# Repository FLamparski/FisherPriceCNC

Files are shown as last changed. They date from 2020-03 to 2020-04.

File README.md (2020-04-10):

# Fisher Price CNC

A desktop, 2D CNC machine made from parts salvaged from a
really terrible 3D priner. This repository contains the
phyiscal CAD design of the machine, electrical and electronic
schematics for any custom boards, and any extra code to make it
run (unlikely to be needed but you never know).

More documentation is currently available on the following
Trello board: https://trello.com/b/17SHQEqY/fisher-price-cnc

## Physical designs - OpenSCAD  - `/scad`

The machine is designed with OpenSCAD, a CAD program that does
away with all of this "drawing" nonsense and instead lets you
use a C-ish programming language to do geometry. The upshot
is that you could treat it like any old source file in git, and
you also have a fairly well understood model for including
libraries.

Speaking of libraries, you will need them. Please install the
following to your OpenSCAD libraries folder:

* [NopSCADlib](https://github.com/nophead/NopSCADlib)

### Assembly instructions

The project leverages NopSCADlib's autogenerated assembly instructions and asset generation. The
instructions are in [`ASSEMBLY.md`](ASSEMBLY.md). Note that these might be a bit variable in quality,
please open an issue if something's not clear. I intend on creating more detailed instructions
towards the end of the project.

To regenerate the assembly instructions, STLs, images, and the bill of materials, use `make_all.ps1`.

## Firmware

This machine uses GRBL v1.1 as its firmware. There is a configuration file, `grbl_config.h`, that is
required to compile and upload GRBL and have it work correctly - it needs to disable homing on the
Z axis because the Z axis does not exist.

Copy the `grbl_config.h` on top of the `config.h` in whatever location you have installed GRBL,
and then reflash through the Arduino IDE.

## Attribution

A number of the parts and a lot of the code for this machine
has been borrowed from other projects. Here's a list:

* Some phyiscal parts have been reused or adapted from the [Prusa i3 MK3s](https://github.com/prusa3d/Original-Prusa-i3/tree/MK3S/Printed-Parts/SCAD) (GPLv3)
* [GRBL](https://github.com/gnea/grbl) is currently used as firmware (GPLv3)

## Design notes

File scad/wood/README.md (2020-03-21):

These parts are not from the normal build, but rather
to fit 30x16 strips of MDF that I found around the flat
and decided to use before ordering the extrusions.

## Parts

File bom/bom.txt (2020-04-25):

Vitamins:
                               X                        
                                                        
                               m                        
                               o           Y            
                               t  X              Y      
                               o        Y  c           Y
    E           L              r  m        a     l  Y   
    l  E  E     a                 o     a  r     i     m
    e  l  l     s        X     a  t     x  r     m  m  o
       e  e     e              n  o     i  i     i  o  t
    b     c     r        c     d  r     s  a     t  t  o
    o  b  t              a  X              g  Y     o  r
    x  o  r     m     X  r     p  h  Y  h  e     s  r   
       x  o  F  o        r  i  u  o     o     i  w     r
 B  b     n  r  d  M  a  i  d  l  l  a  l  b  d  i  l  i
 a  a  t  i  o  u  a  x  a  l  l  d  x  d  a  l  t  e  g
 c  s  o  c  n  l  i  i  g  e  e  e  i  e  s  e  c  f  h
 k  e  p  s  t  e  n  s  e  r  y  r  s  r  e  r  h  t  t
  |  |  |  |  |  |  |  |  |  | 1|  |  |  |  |  |  |  |  |  1 Stepper motor NEMA17 x 40mm
  |  |  |  |  |  |  |  |  |  |  |  |  |  |  |  |  | 1| 1|  2 Stepper motor NEMA17 x 34mm
  |  |  |  |  |  | 2|  |  |  |  |  |  |  |  |  |  |  |  |  2 Belt GT2 x 6mm x 814mm
 1|  |  |  | 1|  |  |  |  |  |  |  |  |  |  |  |  |  |  |  2 Extrusion E3030 x 445mm
  |  |  |  |  |  |  |  |  |  |  |  | 2|  |  |  |  |  |  |  2 Extrusion E3060 x 345mm
  |  |  |  |  |  | 4|  |  |  |  |  |  |  |  |  |  |  |  |  4 Extrusion corner bracket 20
  |  |  |  |  | 1|  |  |  |  |  |  |  |  |  |  |  |  |  |  1 Fan 40mm x 11mm
  |  |  | 1|  |  |  |  |  |  |  |  |  |  |  |  |  |  |  |  1 Terminal block 2 way 3.5mm
  |  |  |  |  | 1|  |  |  |  |  |  |  |  |  |  |  |  |  |  1 laser module
  |  | 1|  |  |  |  |  |  |  |  |  |  |  |  |  |  |  |  |  1 LED 5 mm red
  |  |  |  |  |  |  |  | 2|  |  |  |  |  | 6|  |  |  |  |  8 Linear bearing LM8UU
  |  |  |  |  |  |  |  |  | 1|  | 1|  |  |  |  | 4|  |  |  6 Microswitch SS-01 or SS-5GL
  | 4|  |  |  |  |  |  |  |  |  |  |  |  |  |  | 8|  |  | 12 Nut M2 x 1.6mm 
  | 3|  |  |  |  |  |  | 2|  |  |  |  |  | 2|  |  |  |  |  7 Nut M3 x 2.4mm 
  | 3|  |  |  |  |  |  | 1|  |  |  |  |  |12|  |  |  |  | 16 Nut M3nS 5.5 x 1.8mm 
  |  |  |  |  |  |  |  |  | 1|  |  |  |  |  | 2|  |  |  |  3 Nut M4 x 3.2mm 
  |  |  | 1|  |  |  |  |  |  |  |  |  |  |  |  |  |  |  |  1 Arduino Uno R3
  |  |  | 4|  |  |  |  |  |  |  |  |  |  |  |  |  |  |  |  4 Stepper Motor Driver
  |  |  | 1|  |  |  |  |  |  |  |  |  |  |  |  |  |  |  |  1 Perfboard 80 x 20mm
  |  |  | 8|  |  |  |  |  |  |  |  |  |  |  |  |  |  |  |  8 Pin socket 8 x 1
  |  |  |  |  |  |  |  |  | 1|  |  |  |  |  | 2|  |  |  |  3 Pulley GT2 idler 20 teeth
  |  |  |  |  |  |  |  |  |  | 1|  |  |  |  |  |  | 1| 1|  3 Pulley GT2OB 20 teeth
  |  |  |  |  |  |  |  |  |  |  |  |  | 8|  |  |  |  |  |  8 Smooth rod 8mm x 30mm
  |  |  |  |  |  |  | 2|  |  |  |  |  |  |  |  |  |  |  |  2 Smooth rod 8mm x 343mm
  |  |  |  |  |  |  |  |  |  |  |  | 4|  |  |  |  |  |  |  4 Smooth rod 8mm x 345mm
  |  |  |  |  |  |  |  |  |  |  |  |  |  |  |  | 8|  |  |  8 Screw M2 cap x 10mm
  |  |  |  |  |  |  |  | 2|  |  |  |  |  |  |  |  |  |  |  2 Screw M3 cap x 12mm
  |  |  |  |  |  |  |  | 1|  |  |  |  |  |  |  |  |  |  |  1 Screw M3 cap x 20mm
  |  |  |  |  |  |  |  |  |  |  |  |  |  | 4|  |  |  |  |  4 Screw M3 cap x  6mm
  |  |  |  |  |  |  |  |  |  |  | 3|  |  |  |  |  | 4| 4| 11 Screw M3 cap x  8mm
  |  |  |  |  |  |  |  |  |  | 2|  |  |  |  |  |  |  |  |  2 Screw M3 grub x  6mm
  |  |  |  |  |  |  |  | 3|  |  |  |  |  |  |  |  |  |  |  3 Screw M3 pan x 12mm
  |  |  |  |  |  |  |  | 1|  |  |  |  |  |  |  |  |  |  |  1 Screw M3 pan x  5mm
  |  |  | 3|  |  | 2|  |  |  |  |  |  |  |  |  |  |  |  |  5 Screw M3 pan x  8mm
  |  |  |  |  |  |  |  |  |  |  |  |  | 8|  | 4|  | 2| 2| 16 Screw M4 cap x 10mm
  |  |  |  |  |  |  |  |  | 1|  |  |  |  |  | 2|  |  |  |  3 Screw M4 cap x 20mm
  |  |  |  |  |  | 8|  |  |  |  |  |  |  |  |  | 8|  |  | 16 Screw M4 cap x  8mm
  |  |  |  |  |  |  |  |  |  |  |  |  |  |  |  | 8|  |  |  8 Nut M4 hammer
  |  |  |  |  |  | 8|  |  |  |  |  |  | 8|  | 4|  | 2| 2| 24 Nut M4 sliding T
  |  |  |  |  |  |  |  |  |  |  |  |  |  |  |  |  | 4| 4|  8 Washer star M3 x 0.5mm
  |  | 1|  |  |  |  |  |  |  |  |  |  |  |  |  |  |  |  |  1 Toggle switch CK7101
  |  |  |  |  |  |  |  |  |  |  |  |  |  |  |  |  | 4| 4|  8 Washer  M3 x 7mm x 0.5mm
  |  |  |  |  |  | 8|  |  | 2|  |  |  |  |  | 4|  |  |  | 14 Washer  M4 x 9mm x 0.8mm
  |  |  |  |  |  |  |  | 1|  |  |  |  |  |  |  |  |  |  |  1 Ziptie 2.5mm x 100mm min length
  |  |  |  |  |  |  |  |  |  |  |  |  | 8|  |  |  |  |  |  8 Ziptie 2.5mm x 100mm min length

Printed:
  | 1|  |  |  |  |  |  |  |  |  |  |  |  |  |  |  |  |  |  1 ele_box_base.stl
  |  | 1|  |  |  |  |  |  |  |  |  |  |  |  |  |  |  |  |  1 ele_box_top.stl
 1|  |  |  |  |  |  |  |  |  |  |  |  |  |  |  |  |  |  |  1 ele_bracket.stl
  |  |  |  |  |  |  |  | 1|  |  |  |  |  |  |  |  |  |  |  1 laser_wire_holder.stl
  |  |  |  |  |  |  |  | 1|  |  |  |  |  |  |  |  |  |  |  1 x_carriage_back.stl
  |  |  |  |  |  |  |  | 1|  |  |  |  |  |  |  |  |  |  |  1 x_carriage_front.stl
  |  |  |  |  |  |  |  |  | 1|  |  |  |  |  |  |  |  |  |  1 x_idler.stl
  |  |  |  |  |  |  |  |  |  |  | 1|  |  |  |  |  |  |  |  1 x_motor_holder_mount.stl
  |  |  |  |  |  |  |  |  |  |  |  |  | 8|  |  |  |  |  |  8 y_axis_holder.stl
  |  |  |  |  |  |  |  |  |  |  |  |  |  | 2|  |  |  |  |  2 y_carriage_base.stl
  |  |  |  |  |  | 2|  |  |  |  |  |  |  |  |  |  |  |  |  2 y_carriage_belt_clamp.stl
  |  |  |  |  |  |  |  |  |  |  |  |  |  |  | 2|  |  |  |  2 y_idler.stl
  |  |  |  |  |  |  |  |  |  |  |  |  |  |  |  | 4|  |  |  4 y_limit_switch.stl
  |  |  |  |  |  |  |  |  |  |  |  |  |  | 2|  |  |  |  |  2 y_limit_switch_hitter.stl
  |  |  |  |  |  |  |  |  |  |  |  |  |  |  |  |  | 1|  |  1 y_motor_left_mount.stl
  |  |  |  |  |  |  |  |  |  |  |  |  |  |  |  |  |  | 1|  1 y_motor_right_mount.stl

Assemblies:
  1 back_assembly
  1 ele_box_base_assembly
  1 ele_box_top_assembly
  1 electronics_assembly
  1 front_assembly
  1 laser_module_assembly
  1 main_assembly
  1 x_axis_assembly
  1 x_carriage_assembly
  1 x_idler_assembly
  1 x_motor_and_pulley_assembly
  1 x_motor_holder_assembly
  2 y_axis_assemblies
  8 y_axis_holder_assemblies
  2 y_carriage_base_assemblies
  2 y_idler_assemblies
  4 y_limit_switch_assemblies
  1 y_motor_left_assembly
  1 y_motor_right_assembly

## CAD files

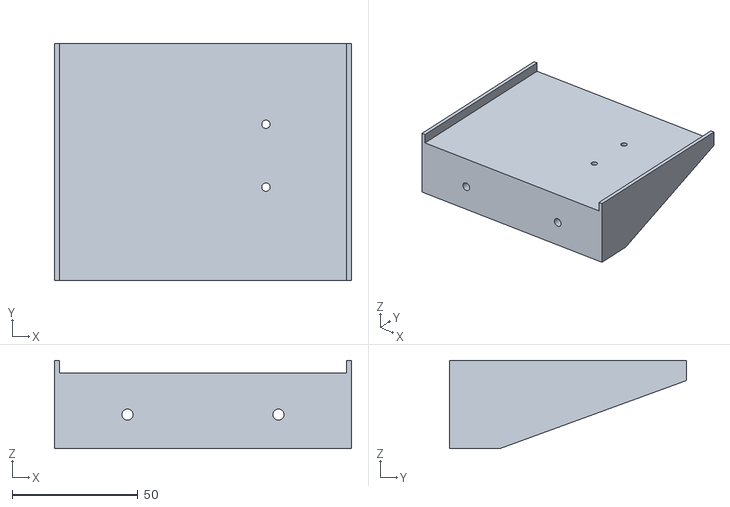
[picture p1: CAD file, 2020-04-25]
stls/ele_bracket.stl
118.0 x 94.0 x 35.0

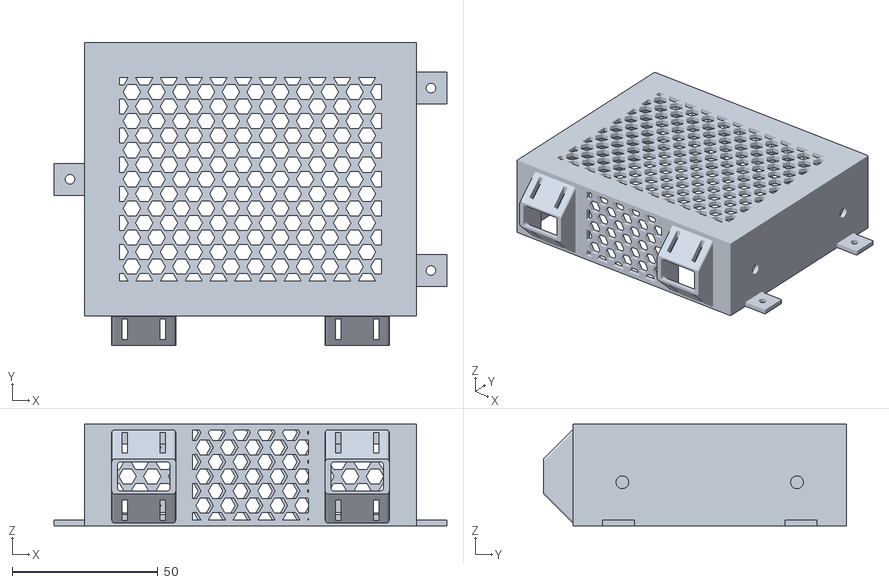
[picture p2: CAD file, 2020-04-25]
stls/ele_box_top.stl
135.0 x 104.1 x 35.0

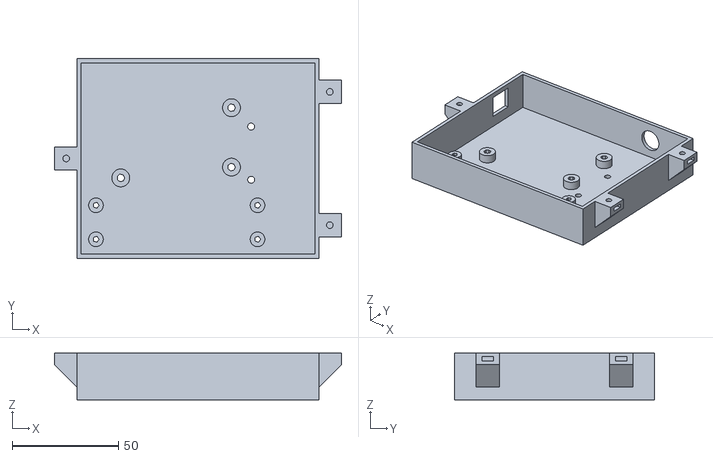
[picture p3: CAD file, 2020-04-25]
stls/ele_box_base.stl
135.0 x 94.0 x 22.0

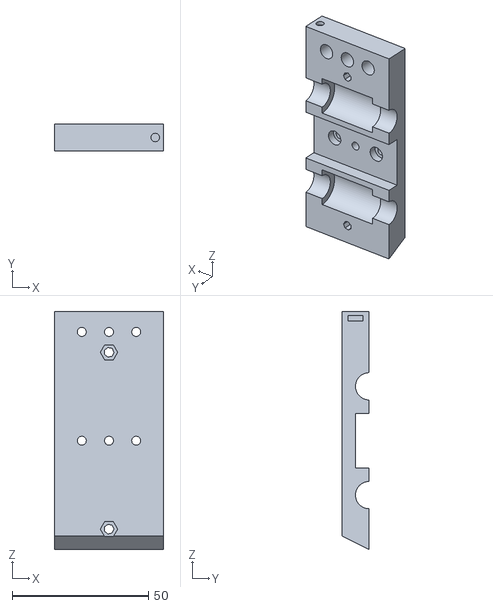
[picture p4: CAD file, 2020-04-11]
stls/x_carriage_front.stl
40.0 x 10.0 x 87.5

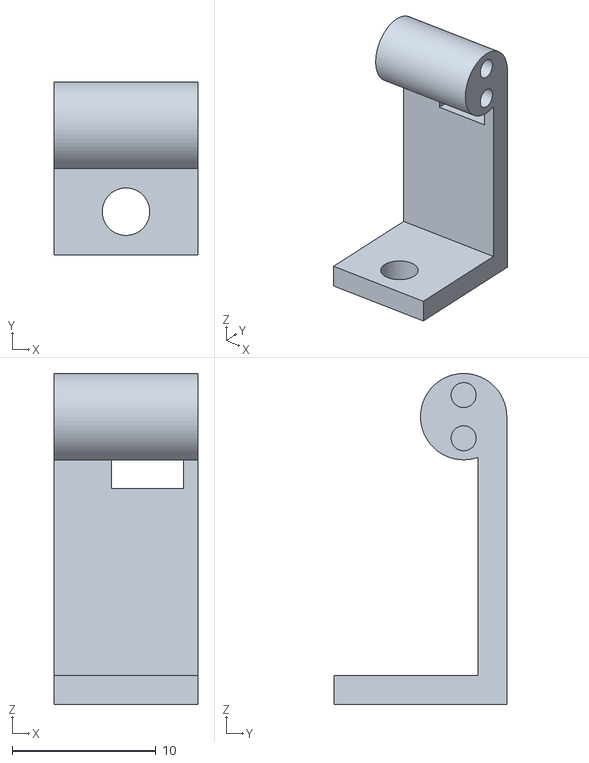
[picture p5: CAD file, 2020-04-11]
stls/laser_wire_holder.stl
10.0 x 12.0 x 23.0

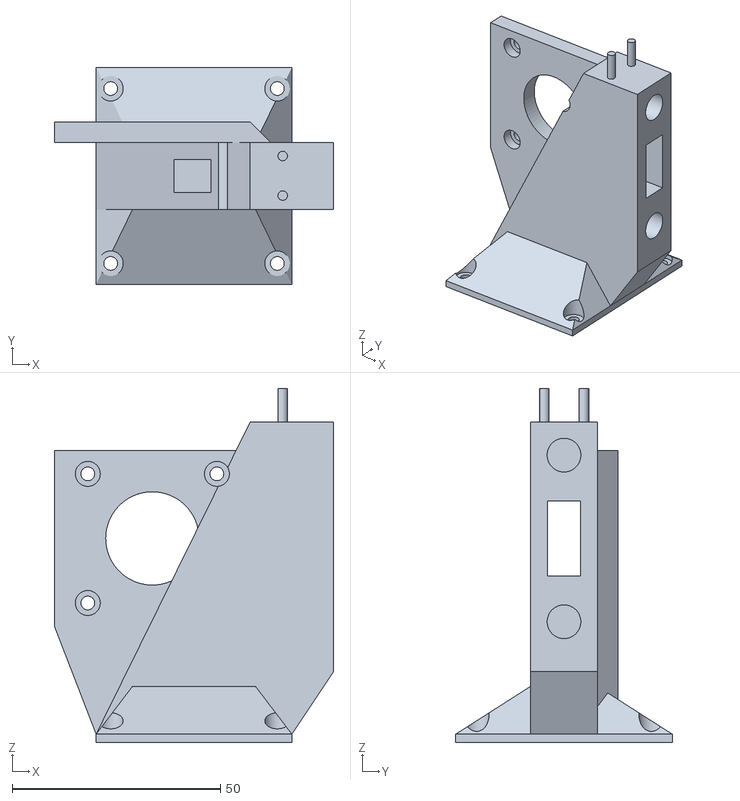
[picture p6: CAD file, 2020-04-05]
stls/x_motor_holder_mount.stl
67.0 x 52.0 x 85.0

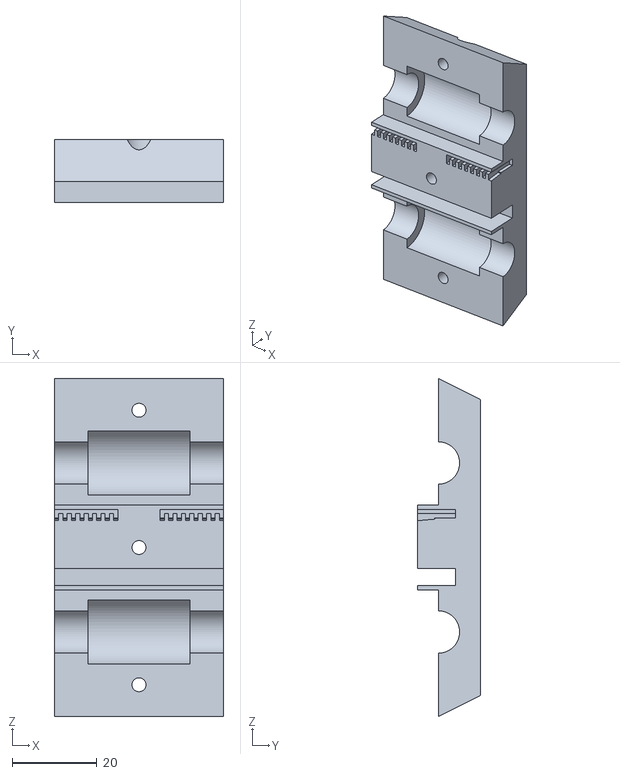
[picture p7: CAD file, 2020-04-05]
stls/x_carriage_back.stl
40.0 x 15.0 x 80.0

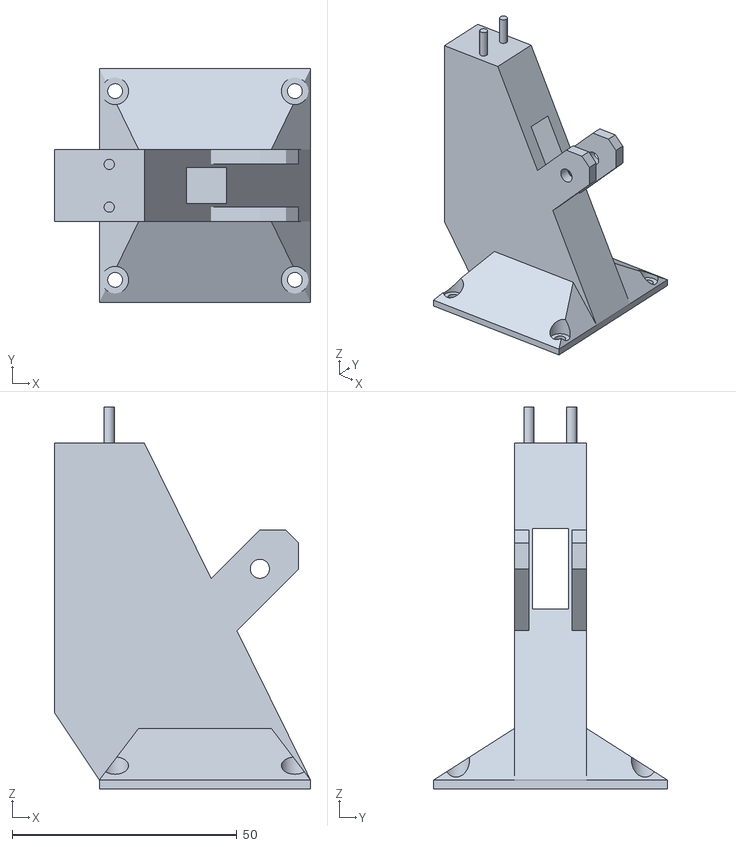
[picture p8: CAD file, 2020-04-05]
stls/x_idler.stl
57.0 x 52.0 x 85.0

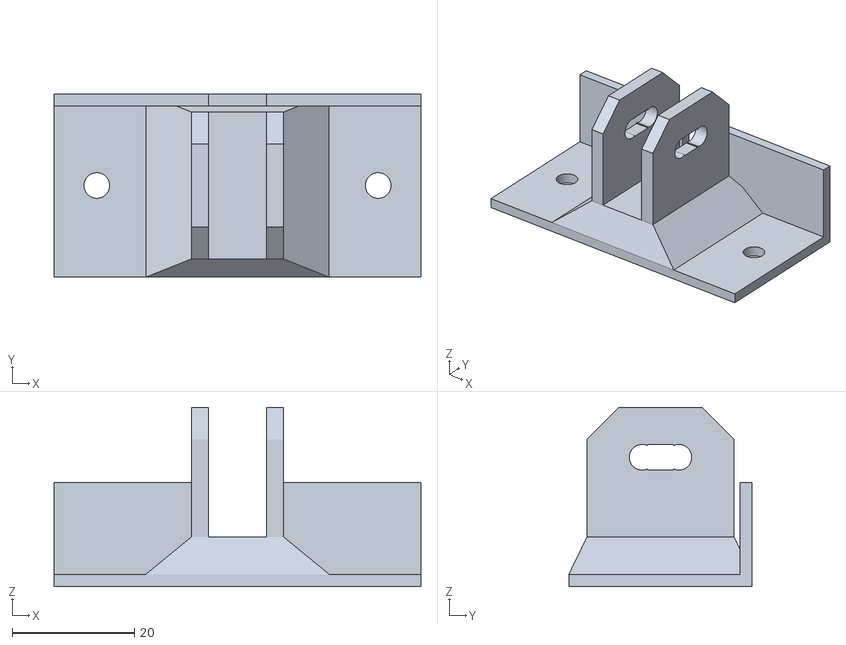
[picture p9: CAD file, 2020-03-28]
stls/y_idler.stl
60.0 x 30.0 x 29.3

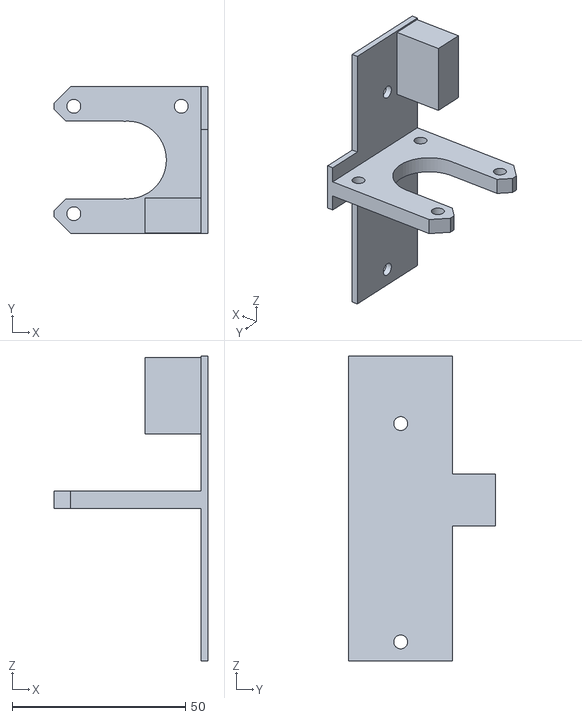
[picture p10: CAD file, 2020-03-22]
stls/y_motor_right_mount.stl
44.3 x 42.3 x 88.0

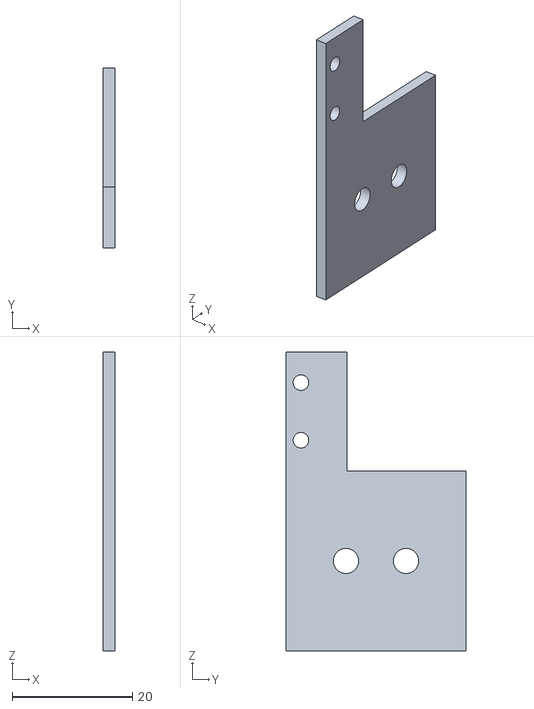
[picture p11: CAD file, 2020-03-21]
stls/y_limit_switch.stl
2.00 x 30.0 x 49.8

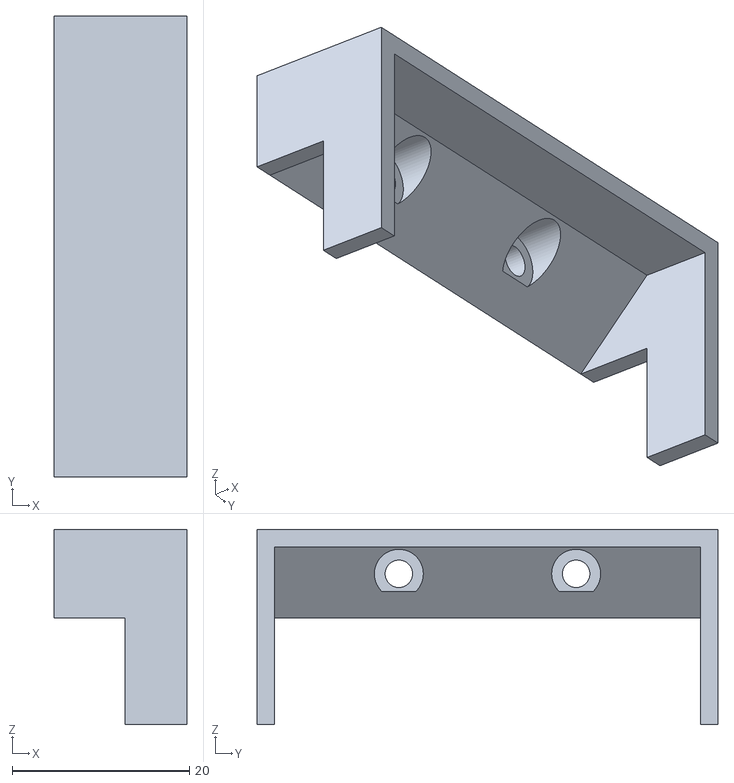
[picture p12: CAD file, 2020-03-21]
stls/y_limit_switch_hitter.stl
15.0 x 52.0 x 22.0

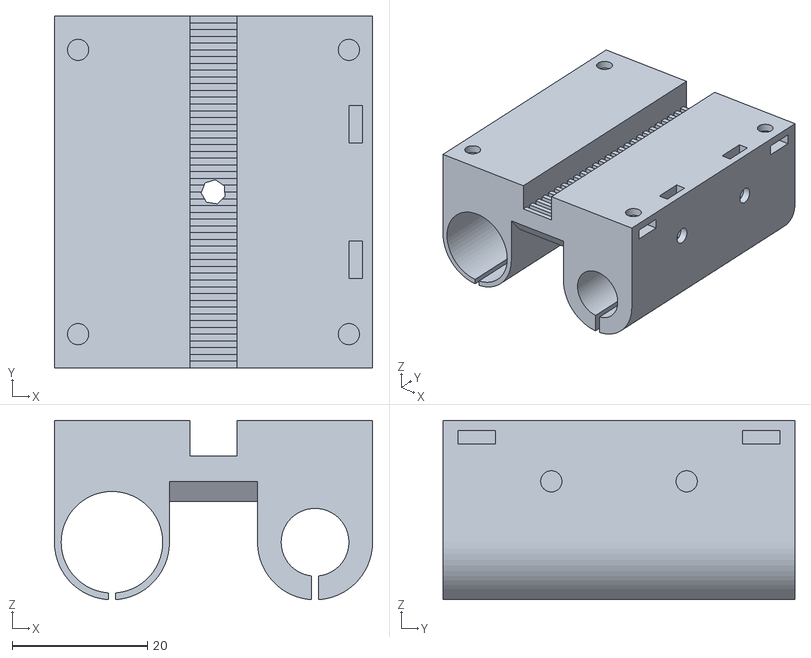
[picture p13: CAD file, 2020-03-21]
stls/y_carriage_base.stl
47.0 x 52.0 x 26.5

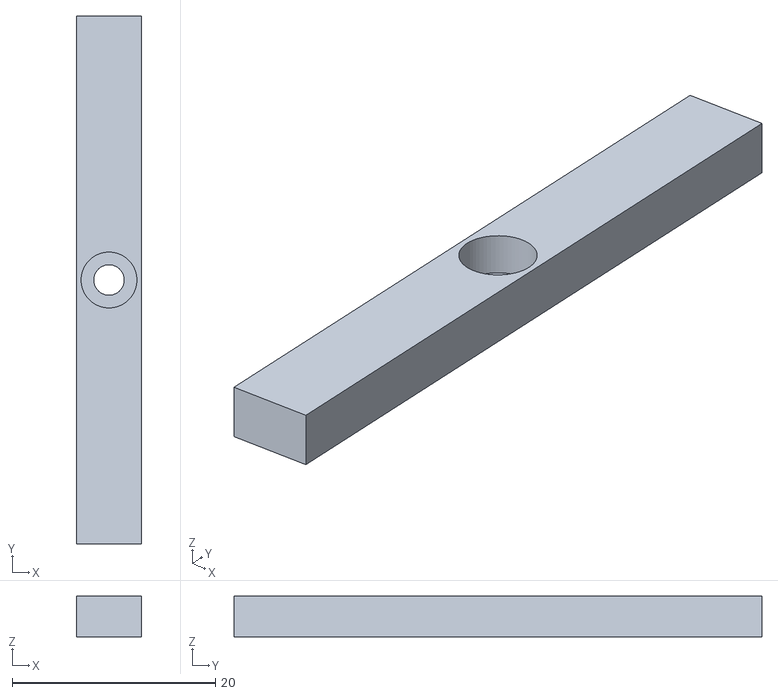
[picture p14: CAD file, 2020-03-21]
stls/y_carriage_belt_clamp.stl
6.40 x 52.0 x 4.00

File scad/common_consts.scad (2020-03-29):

include <NopSCADlib/core.scad>
include <NopSCADlib/vitamins/extrusions.scad>

printed_part_color = "orange";

y_holder_rod_offset = 9 + 8 - 0.5;

rod_length_mm = 345;
inner_margin = -10;
extrusion_type = E3030;
double_width_extrusion_type = E3060;

ew = extrusion_width(extrusion_type);
inner_width = rod_length_mm + inner_margin * 2;
outer_width = inner_width + 2 * 2 * ew;

echo(str("outer_width = ", outer_width));

layer_height = 0.2;

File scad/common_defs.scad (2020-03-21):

include <NopSCADlib/vitamins/nuts.scad>

module pyramid(dim_bottom, dim_top, h) {
    difference() {
        cube(concat(dim_bottom, h));

        x_diff = (dim_bottom[0] - dim_top[0]) / 2;
        x_angle = atan(h / x_diff);
        x_h_diff = sin(x_angle) / x_diff + 10;
        
        rotate([0, 90 - x_angle, 0])
        translate([-dim_bottom[0], 0, 0])
        cube([dim_bottom[0], dim_bottom[1], h + x_h_diff]);

        translate([dim_bottom[0], 0, 0])
        rotate([0, -(90 - x_angle), 0])
        cube([dim_bottom[0], dim_bottom[1], h + x_h_diff]);

        y_diff = (dim_bottom[1] - dim_top[1]) / 2;
        y_angle = atan(h / y_diff);
        y_h_diff = sin(y_angle) / y_diff + 10;
        
        translate([0, dim_bottom[1], 0])
        rotate([90 - y_angle, 0, 0])
        cube([dim_bottom[0], dim_bottom[1], h + y_h_diff]);

        rotate([-(90 - y_angle), 0, 0])
        translate([0, -dim_bottom[1], 0])
        cube([dim_bottom[0], dim_bottom[1], h + y_h_diff]);
    }
}

module square_nut_trap(type, length = 10, depth = 100) {
    width = nut_square_width(type);
    height = nut_square_thickness(type) + layer_height;
    screw_r = nut_square_size(type) / 2;

    union() {
        translate([-width / 2, -width / 2])
        cube([width, length, height]);
        cylinder(r1 = screw_r * 1.05, r2 = screw_r, h = depth);
    }
}

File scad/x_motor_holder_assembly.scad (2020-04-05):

include <NopSCADlib/core.scad>
include <NopSCADlib/vitamins/screws.scad>
include <NopSCADlib/vitamins/stepper_motors.scad>
include <NopSCADlib/vitamins/pulleys.scad>

include <common_consts.scad>
include <common_defs.scad>
include <x_axis_common.scad>

use <y_carriage_base_assembly.scad>

motor_tx = [-10, 13, rod_z_base + x_rods_pitch / 2];

module x_motor_holder_mount_stl() {
    stl("x_motor_holder_mount");

    difference() {
        translate([-y_carriage_base_width() / 2, -y_carriage_base_length() / 2, 0])
        union() {
            x_end_base();

            // support for the motor
            motor_bottom = rod_z_base + x_rods_pitch / 2 - NEMA_width(NEMA17M) / 2;
            motor_top = motor_bottom + NEMA_width(NEMA17M);
            motor_mount_y = x_gantry_thickness / 2 + y_carriage_base_length() / 2 + 5;
            translate([0, motor_mount_y, 0])
            rotate([90, 0, 0])
            linear_extrude(5) {
                polygon([
                    [0, base_thickness],
                    [-10, motor_bottom],
                    [-10, motor_top],
                    [y_carriage_base_width() - 10, motor_top],
                    [y_carriage_base_width() - 10, base_thickness]
                ]);
            }

            // mostly for looks
            translate([y_carriage_base_width() - 5, x_gantry_thickness / 2 + y_carriage_base_length() / 2 + 5, 0])
            rotate([0, 0, 180])
            linear_extrude(motor_top) {
                polygon([
                    [0, 5],
                    [5, 5],
                    [5, 0]
                ]);
            }
        }

        // mounting holes for the motor
        translate([-10, 13, rod_z_base + x_rods_pitch / 2])
        rotate([90, 0, 0]) {
            rbig = NEMA_big_hole(NEMA17M);
            cylinder(r=rbig, h=10, center=true);

            // TODO: make these adjustable?
            NEMA_screw_positions(NEMA17M, n = 3) {
                cylinder(r = screw_clearance_radius(M3_cap_screw), h = 10, center = true);

                translate([0, 0, 12])
                cylinder(r = screw_head_radius(M3_cap_screw) + 0.25, h = 20, center = true);
            }
        }
    }
}

module x_motor_and_pulley_assembly()
assembly("x_motor_and_pulley") {
    NEMA(NEMA17M);

    translate([0, 0, 13])
    pulley_assembly(GT2x20ob_pulley);
}

module x_motor_holder_assembly()
assembly("x_motor_holder") {
    color(printed_part_color)
    x_motor_holder_mount_stl();

    translate(motor_tx)
    rotate([90, 0, 0]) {
        x_motor_and_pulley_assembly();

        NEMA_screw_positions(NEMA17M, n = 3) {
            translate([0, 0, 4])
            screw(M3_cap_screw, 8);
        }
    }

    // Limit switch
    translate([23.9, 0, x_max_height + microswitch_thickness(medium_microswitch) - 1.2])
    rotate([0, 0, -90])
    microswitch(medium_microswitch);
}

if ($preview) {
    x_motor_holder_assembly();
}

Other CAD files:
stls/y_motor_left_mount.stl
stls/y_axis_holder.stl
scad/y_motor_assembly.scad
scad/back_assembly.scad
scad/electronics_assembly.scad
scad/front_assembly.scad
scad/laser.scad
scad/main_assembly.scad
scad/parts/frame_assembly.scad
scad/parts/y_axis_holder_assembly.scad
scad/parts/y_rod_assembly.scad
scad/square_nut_lug.scad
scad/wood/angle_bracket.scad
scad/x_axis_assembly.scad
scad/x_axis_common.scad
scad/x_carriage_assembly.scad
scad/x_idler_assembly.scad
scad/y_axis_assembly.scad
scad/y_axis_holder_assembly.scad
scad/y_carriage_base_assembly.scad
scad/y_idler_assembly.scad
scad/y_limit_switch_assembly.scad
scad/y_rod_assembly.scad

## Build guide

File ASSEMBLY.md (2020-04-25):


# Fisher Price CNC
Fisher Price CNC is a project to turn some parts from the world's worst 3D printer
into a reasonable CNC machine (probably a laser engraver of sorts).

Mechanical parts can be printed out of PLA for testing and PETG for production use.

List of purchases:
* Arduino + GRBL shield + motor drivers: https://smile.amazon.co.uk/gp/product/B06XJKVLG3/
* Belts: https://smile.amazon.co.uk/gp/product/B07JGXG7S2/
* Cap (hex) screws (M2/M3/M4): https://smile.amazon.co.uk/gp/product/B07KCT2F6K/
* M3 square nuts: https://smile.amazon.co.uk/gp/product/B075YSD5TN/
* Pan (phillips) screws (M3): https://smile.amazon.co.uk/gp/product/B07FTDRZRZ/
* LM8UU linear bearings: https://www.ebay.co.uk/itm/LM8UU-8mm-Linear-Bearing-for-Precision-shafts-3D-Printer-CNC-machine/124087391637

If you do not have a Monoprice Mini Delta, you will also need to buy:
* 6x 345x8mm smooth rods, preferably steel
* 3x NEMA17 stepper motors

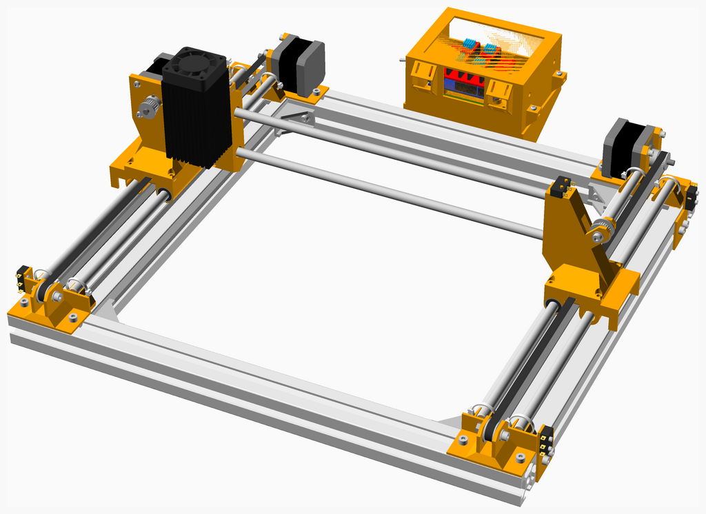
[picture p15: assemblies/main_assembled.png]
Main Assembly


## Table of Contents
1. [Parts list](#Parts_list)
1. [Laser Module Assembly](#laser_module_assembly)
1. [X Carriage Assembly](#x_carriage_assembly)
1. [X Idler Assembly](#x_idler_assembly)
1. [X Motor And Pulley Assembly](#x_motor_and_pulley_assembly)
1. [X Motor Holder Assembly](#x_motor_holder_assembly)
1. [X Axis Assembly](#x_axis_assembly)
1. [Ele Box Top Assembly](#ele_box_top_assembly)
1. [Ele Box Base Assembly](#ele_box_base_assembly)
1. [Electronics Assembly](#electronics_assembly)
1. [Y Motor Right Assembly](#y_motor_right_assembly)
1. [Y Motor Left Assembly](#y_motor_left_assembly)
1. [Back Assembly](#back_assembly)
1. [Y Idler Assembly](#y_idler_assembly)
1. [Front Assembly](#front_assembly)
1. [Y Carriage Base Assembly](#y_carriage_base_assembly)
1. [Y Limit Switch Assembly](#y_limit_switch_assembly)
1. [Y Axis Holder Assembly](#y_axis_holder_assembly)
1. [Y Axis Assembly](#y_axis_assembly)
1. [Main Assembly](#main_assembly)

## Parts list
| <span style="writing-mode: vertical-rl; text-orientation: mixed;">Laser&nbsp;Module</span> | <span style="writing-mode: vertical-rl; text-orientation: mixed;">X&nbsp;Carriage</span> | <span style="writing-mode: vertical-rl; text-orientation: mixed;">X&nbsp;Idler</span> | <span style="writing-mode: vertical-rl; text-orientation: mixed;">X&nbsp;Motor&nbsp;And&nbsp;Pulley</span> | <span style="writing-mode: vertical-rl; text-orientation: mixed;">X&nbsp;Motor&nbsp;Holder</span> | <span style="writing-mode: vertical-rl; text-orientation: mixed;">X&nbsp;Axis</span> | <span style="writing-mode: vertical-rl; text-orientation: mixed;">Ele&nbsp;Box&nbsp;Top</span> | <span style="writing-mode: vertical-rl; text-orientation: mixed;">Ele&nbsp;Box&nbsp;Base</span> | <span style="writing-mode: vertical-rl; text-orientation: mixed;">Electronics</span> | <span style="writing-mode: vertical-rl; text-orientation: mixed;">Y&nbsp;Motor&nbsp;Right</span> | <span style="writing-mode: vertical-rl; text-orientation: mixed;">Y&nbsp;Motor&nbsp;Left</span> | <span style="writing-mode: vertical-rl; text-orientation: mixed;">Back</span> | <span style="writing-mode: vertical-rl; text-orientation: mixed;">Y&nbsp;Idler</span> | <span style="writing-mode: vertical-rl; text-orientation: mixed;">Front</span> | <span style="writing-mode: vertical-rl; text-orientation: mixed;">Y&nbsp;Carriage&nbsp;Base</span> | <span style="writing-mode: vertical-rl; text-orientation: mixed;">Y&nbsp;Limit&nbsp;Switch</span> | <span style="writing-mode: vertical-rl; text-orientation: mixed;">Y&nbsp;Axis&nbsp;Holder</span> | <span style="writing-mode: vertical-rl; text-orientation: mixed;">Y&nbsp;Axis</span> | <span style="writing-mode: vertical-rl; text-orientation: mixed;">Main</span> | <span style="writing-mode: vertical-rl; text-orientation: mixed;">TOTALS</span> |  |
|---:|---:|---:|---:|---:|---:|---:|---:|---:|---:|---:|---:|---:|---:|---:|---:|---:|---:|---:|---:|:---|
|  |  |  |  |  |  |  |  |  |  |  |  |  |  |  |  |  |  |  | | **Vitamins** |
| &nbsp;&nbsp;.&nbsp; | &nbsp;&nbsp;.&nbsp; | &nbsp;&nbsp;.&nbsp; | &nbsp;&nbsp;.&nbsp; | &nbsp;&nbsp;.&nbsp; | &nbsp;&nbsp;.&nbsp; | &nbsp;&nbsp;.&nbsp; | &nbsp;&nbsp;.&nbsp; | &nbsp;&nbsp;1&nbsp; | &nbsp;&nbsp;.&nbsp; | &nbsp;&nbsp;.&nbsp; | &nbsp;&nbsp;.&nbsp; | &nbsp;&nbsp;.&nbsp; | &nbsp;&nbsp;.&nbsp; | &nbsp;&nbsp;.&nbsp; | &nbsp;&nbsp;.&nbsp; | &nbsp;&nbsp;.&nbsp; | &nbsp;&nbsp;.&nbsp; | &nbsp;&nbsp;.&nbsp; |  &nbsp;&nbsp;1&nbsp; | &nbsp;&nbsp; Arduino Uno R3 |
| &nbsp;&nbsp;.&nbsp; | &nbsp;&nbsp;.&nbsp; | &nbsp;&nbsp;.&nbsp; | &nbsp;&nbsp;.&nbsp; | &nbsp;&nbsp;.&nbsp; | &nbsp;&nbsp;.&nbsp; | &nbsp;&nbsp;.&nbsp; | &nbsp;&nbsp;.&nbsp; | &nbsp;&nbsp;.&nbsp; | &nbsp;&nbsp;.&nbsp; | &nbsp;&nbsp;.&nbsp; | &nbsp;&nbsp;.&nbsp; | &nbsp;&nbsp;.&nbsp; | &nbsp;&nbsp;.&nbsp; | &nbsp;&nbsp;.&nbsp; | &nbsp;&nbsp;.&nbsp; | &nbsp;&nbsp;.&nbsp; | &nbsp;&nbsp;.&nbsp; | &nbsp;&nbsp;2&nbsp; |  &nbsp;&nbsp;2&nbsp; | &nbsp;&nbsp; Belt GT2 x 6mm x 814mm |
| &nbsp;&nbsp;.&nbsp; | &nbsp;&nbsp;.&nbsp; | &nbsp;&nbsp;.&nbsp; | &nbsp;&nbsp;.&nbsp; | &nbsp;&nbsp;.&nbsp; | &nbsp;&nbsp;.&nbsp; | &nbsp;&nbsp;.&nbsp; | &nbsp;&nbsp;.&nbsp; | &nbsp;&nbsp;.&nbsp; | &nbsp;&nbsp;.&nbsp; | &nbsp;&nbsp;.&nbsp; | &nbsp;&nbsp;1&nbsp; | &nbsp;&nbsp;.&nbsp; | &nbsp;&nbsp;1&nbsp; | &nbsp;&nbsp;.&nbsp; | &nbsp;&nbsp;.&nbsp; | &nbsp;&nbsp;.&nbsp; | &nbsp;&nbsp;.&nbsp; | &nbsp;&nbsp;.&nbsp; |  &nbsp;&nbsp;2&nbsp; | &nbsp;&nbsp; Extrusion E3030 x 445mm |
| &nbsp;&nbsp;.&nbsp; | &nbsp;&nbsp;.&nbsp; | &nbsp;&nbsp;.&nbsp; | &nbsp;&nbsp;.&nbsp; | &nbsp;&nbsp;.&nbsp; | &nbsp;&nbsp;.&nbsp; | &nbsp;&nbsp;.&nbsp; | &nbsp;&nbsp;.&nbsp; | &nbsp;&nbsp;.&nbsp; | &nbsp;&nbsp;.&nbsp; | &nbsp;&nbsp;.&nbsp; | &nbsp;&nbsp;.&nbsp; | &nbsp;&nbsp;.&nbsp; | &nbsp;&nbsp;.&nbsp; | &nbsp;&nbsp;.&nbsp; | &nbsp;&nbsp;.&nbsp; | &nbsp;&nbsp;.&nbsp; | &nbsp;&nbsp;2&nbsp; | &nbsp;&nbsp;.&nbsp; |  &nbsp;&nbsp;2&nbsp; | &nbsp;&nbsp; Extrusion E3060 x 345mm |
| &nbsp;&nbsp;.&nbsp; | &nbsp;&nbsp;.&nbsp; | &nbsp;&nbsp;.&nbsp; | &nbsp;&nbsp;.&nbsp; | &nbsp;&nbsp;.&nbsp; | &nbsp;&nbsp;.&nbsp; | &nbsp;&nbsp;.&nbsp; | &nbsp;&nbsp;.&nbsp; | &nbsp;&nbsp;.&nbsp; | &nbsp;&nbsp;.&nbsp; | &nbsp;&nbsp;.&nbsp; | &nbsp;&nbsp;.&nbsp; | &nbsp;&nbsp;.&nbsp; | &nbsp;&nbsp;.&nbsp; | &nbsp;&nbsp;.&nbsp; | &nbsp;&nbsp;.&nbsp; | &nbsp;&nbsp;.&nbsp; | &nbsp;&nbsp;.&nbsp; | &nbsp;&nbsp;4&nbsp; |  &nbsp;&nbsp;4&nbsp; | &nbsp;&nbsp; Extrusion corner bracket 20 |
| &nbsp;&nbsp;1&nbsp; | &nbsp;&nbsp;.&nbsp; | &nbsp;&nbsp;.&nbsp; | &nbsp;&nbsp;.&nbsp; | &nbsp;&nbsp;.&nbsp; | &nbsp;&nbsp;.&nbsp; | &nbsp;&nbsp;.&nbsp; | &nbsp;&nbsp;.&nbsp; | &nbsp;&nbsp;.&nbsp; | &nbsp;&nbsp;.&nbsp; | &nbsp;&nbsp;.&nbsp; | &nbsp;&nbsp;.&nbsp; | &nbsp;&nbsp;.&nbsp; | &nbsp;&nbsp;.&nbsp; | &nbsp;&nbsp;.&nbsp; | &nbsp;&nbsp;.&nbsp; | &nbsp;&nbsp;.&nbsp; | &nbsp;&nbsp;.&nbsp; | &nbsp;&nbsp;.&nbsp; |  &nbsp;&nbsp;1&nbsp; | &nbsp;&nbsp; Fan 40mm x 11mm |
| &nbsp;&nbsp;.&nbsp; | &nbsp;&nbsp;.&nbsp; | &nbsp;&nbsp;.&nbsp; | &nbsp;&nbsp;.&nbsp; | &nbsp;&nbsp;.&nbsp; | &nbsp;&nbsp;.&nbsp; | &nbsp;&nbsp;1&nbsp; | &nbsp;&nbsp;.&nbsp; | &nbsp;&nbsp;.&nbsp; | &nbsp;&nbsp;.&nbsp; | &nbsp;&nbsp;.&nbsp; | &nbsp;&nbsp;.&nbsp; | &nbsp;&nbsp;.&nbsp; | &nbsp;&nbsp;.&nbsp; | &nbsp;&nbsp;.&nbsp; | &nbsp;&nbsp;.&nbsp; | &nbsp;&nbsp;.&nbsp; | &nbsp;&nbsp;.&nbsp; | &nbsp;&nbsp;.&nbsp; |  &nbsp;&nbsp;1&nbsp; | &nbsp;&nbsp; LED 5 mm red |
| &nbsp;&nbsp;.&nbsp; | &nbsp;&nbsp;2&nbsp; | &nbsp;&nbsp;.&nbsp; | &nbsp;&nbsp;.&nbsp; | &nbsp;&nbsp;.&nbsp; | &nbsp;&nbsp;.&nbsp; | &nbsp;&nbsp;.&nbsp; | &nbsp;&nbsp;.&nbsp; | &nbsp;&nbsp;.&nbsp; | &nbsp;&nbsp;.&nbsp; | &nbsp;&nbsp;.&nbsp; | &nbsp;&nbsp;.&nbsp; | &nbsp;&nbsp;.&nbsp; | &nbsp;&nbsp;.&nbsp; | &nbsp;&nbsp;6&nbsp; | &nbsp;&nbsp;.&nbsp; | &nbsp;&nbsp;.&nbsp; | &nbsp;&nbsp;.&nbsp; | &nbsp;&nbsp;.&nbsp; |  &nbsp;&nbsp;8&nbsp; | &nbsp;&nbsp; Linear bearing LM8UU |
| &nbsp;&nbsp;.&nbsp; | &nbsp;&nbsp;.&nbsp; | &nbsp;&nbsp;1&nbsp; | &nbsp;&nbsp;.&nbsp; | &nbsp;&nbsp;1&nbsp; | &nbsp;&nbsp;.&nbsp; | &nbsp;&nbsp;.&nbsp; | &nbsp;&nbsp;.&nbsp; | &nbsp;&nbsp;.&nbsp; | &nbsp;&nbsp;.&nbsp; | &nbsp;&nbsp;.&nbsp; | &nbsp;&nbsp;.&nbsp; | &nbsp;&nbsp;.&nbsp; | &nbsp;&nbsp;.&nbsp; | &nbsp;&nbsp;.&nbsp; | &nbsp;&nbsp;4&nbsp; | &nbsp;&nbsp;.&nbsp; | &nbsp;&nbsp;.&nbsp; | &nbsp;&nbsp;.&nbsp; |  &nbsp;&nbsp;6&nbsp; | &nbsp;&nbsp; Microswitch SS-01 or SS-5GL |
| &nbsp;&nbsp;.&nbsp; | &nbsp;&nbsp;.&nbsp; | &nbsp;&nbsp;.&nbsp; | &nbsp;&nbsp;.&nbsp; | &nbsp;&nbsp;.&nbsp; | &nbsp;&nbsp;.&nbsp; | &nbsp;&nbsp;.&nbsp; | &nbsp;&nbsp;4&nbsp; | &nbsp;&nbsp;.&nbsp; | &nbsp;&nbsp;.&nbsp; | &nbsp;&nbsp;.&nbsp; | &nbsp;&nbsp;.&nbsp; | &nbsp;&nbsp;.&nbsp; | &nbsp;&nbsp;.&nbsp; | &nbsp;&nbsp;.&nbsp; | &nbsp;&nbsp;8&nbsp; | &nbsp;&nbsp;.&nbsp; | &nbsp;&nbsp;.&nbsp; | &nbsp;&nbsp;.&nbsp; |  &nbsp;&nbsp;12&nbsp; | &nbsp;&nbsp; Nut M2 x 1.6mm  |
| &nbsp;&nbsp;.&nbsp; | &nbsp;&nbsp;2&nbsp; | &nbsp;&nbsp;.&nbsp; | &nbsp;&nbsp;.&nbsp; | &nbsp;&nbsp;.&nbsp; | &nbsp;&nbsp;.&nbsp; | &nbsp;&nbsp;.&nbsp; | &nbsp;&nbsp;3&nbsp; | &nbsp;&nbsp;.&nbsp; | &nbsp;&nbsp;.&nbsp; | &nbsp;&nbsp;.&nbsp; | &nbsp;&nbsp;.&nbsp; | &nbsp;&nbsp;.&nbsp; | &nbsp;&nbsp;.&nbsp; | &nbsp;&nbsp;2&nbsp; | &nbsp;&nbsp;.&nbsp; | &nbsp;&nbsp;.&nbsp; | &nbsp;&nbsp;.&nbsp; | &nbsp;&nbsp;.&nbsp; |  &nbsp;&nbsp;7&nbsp; | &nbsp;&nbsp; Nut M3 x 2.4mm  |
| &nbsp;&nbsp;.&nbsp; | &nbsp;&nbsp;1&nbsp; | &nbsp;&nbsp;.&nbsp; | &nbsp;&nbsp;.&nbsp; | &nbsp;&nbsp;.&nbsp; | &nbsp;&nbsp;.&nbsp; | &nbsp;&nbsp;.&nbsp; | &nbsp;&nbsp;3&nbsp; | &nbsp;&nbsp;.&nbsp; | &nbsp;&nbsp;.&nbsp; | &nbsp;&nbsp;.&nbsp; | &nbsp;&nbsp;.&nbsp; | &nbsp;&nbsp;.&nbsp; | &nbsp;&nbsp;.&nbsp; | &nbsp;&nbsp;12&nbsp; | &nbsp;&nbsp;.&nbsp; | &nbsp;&nbsp;.&nbsp; | &nbsp;&nbsp;.&nbsp; | &nbsp;&nbsp;.&nbsp; |  &nbsp;&nbsp;16&nbsp; | &nbsp;&nbsp; Nut M3nS 5.5 x 1.8mm  |
| &nbsp;&nbsp;.&nbsp; | &nbsp;&nbsp;.&nbsp; | &nbsp;&nbsp;.&nbsp; | &nbsp;&nbsp;.&nbsp; | &nbsp;&nbsp;.&nbsp; | &nbsp;&nbsp;.&nbsp; | &nbsp;&nbsp;.&nbsp; | &nbsp;&nbsp;.&nbsp; | &nbsp;&nbsp;.&nbsp; | &nbsp;&nbsp;.&nbsp; | &nbsp;&nbsp;.&nbsp; | &nbsp;&nbsp;.&nbsp; | &nbsp;&nbsp;.&nbsp; | &nbsp;&nbsp;.&nbsp; | &nbsp;&nbsp;.&nbsp; | &nbsp;&nbsp;8&nbsp; | &nbsp;&nbsp;.&nbsp; | &nbsp;&nbsp;.&nbsp; | &nbsp;&nbsp;.&nbsp; |  &nbsp;&nbsp;8&nbsp; | &nbsp;&nbsp; Nut M4 hammer |
| &nbsp;&nbsp;.&nbsp; | &nbsp;&nbsp;.&nbsp; | &nbsp;&nbsp;.&nbsp; | &nbsp;&nbsp;.&nbsp; | &nbsp;&nbsp;.&nbsp; | &nbsp;&nbsp;.&nbsp; | &nbsp;&nbsp;.&nbsp; | &nbsp;&nbsp;.&nbsp; | &nbsp;&nbsp;.&nbsp; | &nbsp;&nbsp;2&nbsp; | &nbsp;&nbsp;2&nbsp; | &nbsp;&nbsp;.&nbsp; | &nbsp;&nbsp;4&nbsp; | &nbsp;&nbsp;.&nbsp; | &nbsp;&nbsp;.&nbsp; | &nbsp;&nbsp;.&nbsp; | &nbsp;&nbsp;8&nbsp; | &nbsp;&nbsp;.&nbsp; | &nbsp;&nbsp;8&nbsp; |  &nbsp;&nbsp;24&nbsp; | &nbsp;&nbsp; Nut M4 sliding T |
| &nbsp;&nbsp;.&nbsp; | &nbsp;&nbsp;.&nbsp; | &nbsp;&nbsp;1&nbsp; | &nbsp;&nbsp;.&nbsp; | &nbsp;&nbsp;.&nbsp; | &nbsp;&nbsp;.&nbsp; | &nbsp;&nbsp;.&nbsp; | &nbsp;&nbsp;.&nbsp; | &nbsp;&nbsp;.&nbsp; | &nbsp;&nbsp;.&nbsp; | &nbsp;&nbsp;.&nbsp; | &nbsp;&nbsp;.&nbsp; | &nbsp;&nbsp;2&nbsp; | &nbsp;&nbsp;.&nbsp; | &nbsp;&nbsp;.&nbsp; | &nbsp;&nbsp;.&nbsp; | &nbsp;&nbsp;.&nbsp; | &nbsp;&nbsp;.&nbsp; | &nbsp;&nbsp;.&nbsp; |  &nbsp;&nbsp;3&nbsp; | &nbsp;&nbsp; Nut M4 x 3.2mm  |
| &nbsp;&nbsp;.&nbsp; | &nbsp;&nbsp;.&nbsp; | &nbsp;&nbsp;.&nbsp; | &nbsp;&nbsp;.&nbsp; | &nbsp;&nbsp;.&nbsp; | &nbsp;&nbsp;.&nbsp; | &nbsp;&nbsp;.&nbsp; | &nbsp;&nbsp;.&nbsp; | &nbsp;&nbsp;1&nbsp; | &nbsp;&nbsp;.&nbsp; | &nbsp;&nbsp;.&nbsp; | &nbsp;&nbsp;.&nbsp; | &nbsp;&nbsp;.&nbsp; | &nbsp;&nbsp;.&nbsp; | &nbsp;&nbsp;.&nbsp; | &nbsp;&nbsp;.&nbsp; | &nbsp;&nbsp;.&nbsp; | &nbsp;&nbsp;.&nbsp; | &nbsp;&nbsp;.&nbsp; |  &nbsp;&nbsp;1&nbsp; | &nbsp;&nbsp; Perfboard 80 x 20mm |
| &nbsp;&nbsp;.&nbsp; | &nbsp;&nbsp;.&nbsp; | &nbsp;&nbsp;.&nbsp; | &nbsp;&nbsp;.&nbsp; | &nbsp;&nbsp;.&nbsp; | &nbsp;&nbsp;.&nbsp; | &nbsp;&nbsp;.&nbsp; | &nbsp;&nbsp;.&nbsp; | &nbsp;&nbsp;8&nbsp; | &nbsp;&nbsp;.&nbsp; | &nbsp;&nbsp;.&nbsp; | &nbsp;&nbsp;.&nbsp; | &nbsp;&nbsp;.&nbsp; | &nbsp;&nbsp;.&nbsp; | &nbsp;&nbsp;.&nbsp; | &nbsp;&nbsp;.&nbsp; | &nbsp;&nbsp;.&nbsp; | &nbsp;&nbsp;.&nbsp; | &nbsp;&nbsp;.&nbsp; |  &nbsp;&nbsp;8&nbsp; | &nbsp;&nbsp; Pin socket 8 x 1 |
| &nbsp;&nbsp;.&nbsp; | &nbsp;&nbsp;.&nbsp; | &nbsp;&nbsp;1&nbsp; | &nbsp;&nbsp;.&nbsp; | &nbsp;&nbsp;.&nbsp; | &nbsp;&nbsp;.&nbsp; | &nbsp;&nbsp;.&nbsp; | &nbsp;&nbsp;.&nbsp; | &nbsp;&nbsp;.&nbsp; | &nbsp;&nbsp;.&nbsp; | &nbsp;&nbsp;.&nbsp; | &nbsp;&nbsp;.&nbsp; | &nbsp;&nbsp;2&nbsp; | &nbsp;&nbsp;.&nbsp; | &nbsp;&nbsp;.&nbsp; | &nbsp;&nbsp;.&nbsp; | &nbsp;&nbsp;.&nbsp; | &nbsp;&nbsp;.&nbsp; | &nbsp;&nbsp;.&nbsp; |  &nbsp;&nbsp;3&nbsp; | &nbsp;&nbsp; Pulley GT2 idler 20 teeth |
| &nbsp;&nbsp;.&nbsp; | &nbsp;&nbsp;.&nbsp; | &nbsp;&nbsp;.&nbsp; | &nbsp;&nbsp;1&nbsp; | &nbsp;&nbsp;.&nbsp; | &nbsp;&nbsp;.&nbsp; | &nbsp;&nbsp;.&nbsp; | &nbsp;&nbsp;.&nbsp; | &nbsp;&nbsp;.&nbsp; | &nbsp;&nbsp;1&nbsp; | &nbsp;&nbsp;1&nbsp; | &nbsp;&nbsp;.&nbsp; | &nbsp;&nbsp;.&nbsp; | &nbsp;&nbsp;.&nbsp; | &nbsp;&nbsp;.&nbsp; | &nbsp;&nbsp;.&nbsp; | &nbsp;&nbsp;.&nbsp; | &nbsp;&nbsp;.&nbsp; | &nbsp;&nbsp;.&nbsp; |  &nbsp;&nbsp;3&nbsp; | &nbsp;&nbsp; Pulley GT2OB 20 teeth |
| &nbsp;&nbsp;.&nbsp; | &nbsp;&nbsp;.&nbsp; | &nbsp;&nbsp;.&nbsp; | &nbsp;&nbsp;.&nbsp; | &nbsp;&nbsp;.&nbsp; | &nbsp;&nbsp;.&nbsp; | &nbsp;&nbsp;.&nbsp; | &nbsp;&nbsp;.&nbsp; | &nbsp;&nbsp;.&nbsp; | &nbsp;&nbsp;.&nbsp; | &nbsp;&nbsp;.&nbsp; | &nbsp;&nbsp;.&nbsp; | &nbsp;&nbsp;.&nbsp; | &nbsp;&nbsp;.&nbsp; | &nbsp;&nbsp;.&nbsp; | &nbsp;&nbsp;8&nbsp; | &nbsp;&nbsp;.&nbsp; | &nbsp;&nbsp;.&nbsp; | &nbsp;&nbsp;.&nbsp; |  &nbsp;&nbsp;8&nbsp; | &nbsp;&nbsp; Screw M2 cap x 10mm |
| &nbsp;&nbsp;.&nbsp; | &nbsp;&nbsp;.&nbsp; | &nbsp;&nbsp;.&nbsp; | &nbsp;&nbsp;.&nbsp; | &nbsp;&nbsp;.&nbsp; | &nbsp;&nbsp;.&nbsp; | &nbsp;&nbsp;.&nbsp; | &nbsp;&nbsp;.&nbsp; | &nbsp;&nbsp;.&nbsp; | &nbsp;&nbsp;.&nbsp; | &nbsp;&nbsp;.&nbsp; | &nbsp;&nbsp;.&nbsp; | &nbsp;&nbsp;.&nbsp; | &nbsp;&nbsp;.&nbsp; | &nbsp;&nbsp;4&nbsp; | &nbsp;&nbsp;.&nbsp; | &nbsp;&nbsp;.&nbsp; | &nbsp;&nbsp;.&nbsp; | &nbsp;&nbsp;.&nbsp; |  &nbsp;&nbsp;4&nbsp; | &nbsp;&nbsp; Screw M3 cap x  6mm |
| &nbsp;&nbsp;.&nbsp; | &nbsp;&nbsp;.&nbsp; | &nbsp;&nbsp;.&nbsp; | &nbsp;&nbsp;.&nbsp; | &nbsp;&nbsp;3&nbsp; | &nbsp;&nbsp;.&nbsp; | &nbsp;&nbsp;.&nbsp; | &nbsp;&nbsp;.&nbsp; | &nbsp;&nbsp;.&nbsp; | &nbsp;&nbsp;4&nbsp; | &nbsp;&nbsp;4&nbsp; | &nbsp;&nbsp;.&nbsp; | &nbsp;&nbsp;.&nbsp; | &nbsp;&nbsp;.&nbsp; | &nbsp;&nbsp;.&nbsp; | &nbsp;&nbsp;.&nbsp; | &nbsp;&nbsp;.&nbsp; | &nbsp;&nbsp;.&nbsp; | &nbsp;&nbsp;.&nbsp; |  &nbsp;&nbsp;11&nbsp; | &nbsp;&nbsp; Screw M3 cap x  8mm |
| &nbsp;&nbsp;.&nbsp; | &nbsp;&nbsp;2&nbsp; | &nbsp;&nbsp;.&nbsp; | &nbsp;&nbsp;.&nbsp; | &nbsp;&nbsp;.&nbsp; | &nbsp;&nbsp;.&nbsp; | &nbsp;&nbsp;.&nbsp; | &nbsp;&nbsp;.&nbsp; | &nbsp;&nbsp;.&nbsp; | &nbsp;&nbsp;.&nbsp; | &nbsp;&nbsp;.&nbsp; | &nbsp;&nbsp;.&nbsp; | &nbsp;&nbsp;.&nbsp; | &nbsp;&nbsp;.&nbsp; | &nbsp;&nbsp;.&nbsp; | &nbsp;&nbsp;.&nbsp; | &nbsp;&nbsp;.&nbsp; | &nbsp;&nbsp;.&nbsp; | &nbsp;&nbsp;.&nbsp; |  &nbsp;&nbsp;2&nbsp; | &nbsp;&nbsp; Screw M3 cap x 12mm |
| &nbsp;&nbsp;.&nbsp; | &nbsp;&nbsp;1&nbsp; | &nbsp;&nbsp;.&nbsp; | &nbsp;&nbsp;.&nbsp; | &nbsp;&nbsp;.&nbsp; | &nbsp;&nbsp;.&nbsp; | &nbsp;&nbsp;.&nbsp; | &nbsp;&nbsp;.&nbsp; | &nbsp;&nbsp;.&nbsp; | &nbsp;&nbsp;.&nbsp; | &nbsp;&nbsp;.&nbsp; | &nbsp;&nbsp;.&nbsp; | &nbsp;&nbsp;.&nbsp; | &nbsp;&nbsp;.&nbsp; | &nbsp;&nbsp;.&nbsp; | &nbsp;&nbsp;.&nbsp; | &nbsp;&nbsp;.&nbsp; | &nbsp;&nbsp;.&nbsp; | &nbsp;&nbsp;.&nbsp; |  &nbsp;&nbsp;1&nbsp; | &nbsp;&nbsp; Screw M3 cap x 20mm |
| &nbsp;&nbsp;.&nbsp; | &nbsp;&nbsp;.&nbsp; | &nbsp;&nbsp;.&nbsp; | &nbsp;&nbsp;2&nbsp; | &nbsp;&nbsp;.&nbsp; | &nbsp;&nbsp;.&nbsp; | &nbsp;&nbsp;.&nbsp; | &nbsp;&nbsp;.&nbsp; | &nbsp;&nbsp;.&nbsp; | &nbsp;&nbsp;.&nbsp; | &nbsp;&nbsp;.&nbsp; | &nbsp;&nbsp;.&nbsp; | &nbsp;&nbsp;.&nbsp; | &nbsp;&nbsp;.&nbsp; | &nbsp;&nbsp;.&nbsp; | &nbsp;&nbsp;.&nbsp; | &nbsp;&nbsp;.&nbsp; | &nbsp;&nbsp;.&nbsp; | &nbsp;&nbsp;.&nbsp; |  &nbsp;&nbsp;2&nbsp; | &nbsp;&nbsp; Screw M3 grub x  6mm |
| &nbsp;&nbsp;.&nbsp; | &nbsp;&nbsp;1&nbsp; | &nbsp;&nbsp;.&nbsp; | &nbsp;&nbsp;.&nbsp; | &nbsp;&nbsp;.&nbsp; | &nbsp;&nbsp;.&nbsp; | &nbsp;&nbsp;.&nbsp; | &nbsp;&nbsp;.&nbsp; | &nbsp;&nbsp;.&nbsp; | &nbsp;&nbsp;.&nbsp; | &nbsp;&nbsp;.&nbsp; | &nbsp;&nbsp;.&nbsp; | &nbsp;&nbsp;.&nbsp; | &nbsp;&nbsp;.&nbsp; | &nbsp;&nbsp;.&nbsp; | &nbsp;&nbsp;.&nbsp; | &nbsp;&nbsp;.&nbsp; | &nbsp;&nbsp;.&nbsp; | &nbsp;&nbsp;.&nbsp; |  &nbsp;&nbsp;1&nbsp; | &nbsp;&nbsp; Screw M3 pan x  5mm |
| &nbsp;&nbsp;.&nbsp; | &nbsp;&nbsp;.&nbsp; | &nbsp;&nbsp;.&nbsp; | &nbsp;&nbsp;.&nbsp; | &nbsp;&nbsp;.&nbsp; | &nbsp;&nbsp;.&nbsp; | &nbsp;&nbsp;.&nbsp; | &nbsp;&nbsp;.&nbsp; | &nbsp;&nbsp;3&nbsp; | &nbsp;&nbsp;.&nbsp; | &nbsp;&nbsp;.&nbsp; | &nbsp;&nbsp;.&nbsp; | &nbsp;&nbsp;.&nbsp; | &nbsp;&nbsp;.&nbsp; | &nbsp;&nbsp;.&nbsp; | &nbsp;&nbsp;.&nbsp; | &nbsp;&nbsp;.&nbsp; | &nbsp;&nbsp;.&nbsp; | &nbsp;&nbsp;2&nbsp; |  &nbsp;&nbsp;5&nbsp; | &nbsp;&nbsp; Screw M3 pan x  8mm |
| &nbsp;&nbsp;.&nbsp; | &nbsp;&nbsp;3&nbsp; | &nbsp;&nbsp;.&nbsp; | &nbsp;&nbsp;.&nbsp; | &nbsp;&nbsp;.&nbsp; | &nbsp;&nbsp;.&nbsp; | &nbsp;&nbsp;.&nbsp; | &nbsp;&nbsp;.&nbsp; | &nbsp;&nbsp;.&nbsp; | &nbsp;&nbsp;.&nbsp; | &nbsp;&nbsp;.&nbsp; | &nbsp;&nbsp;.&nbsp; | &nbsp;&nbsp;.&nbsp; | &nbsp;&nbsp;.&nbsp; | &nbsp;&nbsp;.&nbsp; | &nbsp;&nbsp;.&nbsp; | &nbsp;&nbsp;.&nbsp; | &nbsp;&nbsp;.&nbsp; | &nbsp;&nbsp;.&nbsp; |  &nbsp;&nbsp;3&nbsp; | &nbsp;&nbsp; Screw M3 pan x 12mm |
| &nbsp;&nbsp;.&nbsp; | &nbsp;&nbsp;.&nbsp; | &nbsp;&nbsp;.&nbsp; | &nbsp;&nbsp;.&nbsp; | &nbsp;&nbsp;.&nbsp; | &nbsp;&nbsp;.&nbsp; | &nbsp;&nbsp;.&nbsp; | &nbsp;&nbsp;.&nbsp; | &nbsp;&nbsp;.&nbsp; | &nbsp;&nbsp;.&nbsp; | &nbsp;&nbsp;.&nbsp; | &nbsp;&nbsp;.&nbsp; | &nbsp;&nbsp;.&nbsp; | &nbsp;&nbsp;.&nbsp; | &nbsp;&nbsp;.&nbsp; | &nbsp;&nbsp;8&nbsp; | &nbsp;&nbsp;.&nbsp; | &nbsp;&nbsp;.&nbsp; | &nbsp;&nbsp;8&nbsp; |  &nbsp;&nbsp;16&nbsp; | &nbsp;&nbsp; Screw M4 cap x  8mm |
| &nbsp;&nbsp;.&nbsp; | &nbsp;&nbsp;.&nbsp; | &nbsp;&nbsp;.&nbsp; | &nbsp;&nbsp;.&nbsp; | &nbsp;&nbsp;.&nbsp; | &nbsp;&nbsp;.&nbsp; | &nbsp;&nbsp;.&nbsp; | &nbsp;&nbsp;.&nbsp; | &nbsp;&nbsp;.&nbsp; | &nbsp;&nbsp;2&nbsp; | &nbsp;&nbsp;2&nbsp; | &nbsp;&nbsp;.&nbsp; | &nbsp;&nbsp;4&nbsp; | &nbsp;&nbsp;.&nbsp; | &nbsp;&nbsp;.&nbsp; | &nbsp;&nbsp;.&nbsp; | &nbsp;&nbsp;8&nbsp; | &nbsp;&nbsp;.&nbsp; | &nbsp;&nbsp;.&nbsp; |  &nbsp;&nbsp;16&nbsp; | &nbsp;&nbsp; Screw M4 cap x 10mm |
| &nbsp;&nbsp;.&nbsp; | &nbsp;&nbsp;.&nbsp; | &nbsp;&nbsp;1&nbsp; | &nbsp;&nbsp;.&nbsp; | &nbsp;&nbsp;.&nbsp; | &nbsp;&nbsp;.&nbsp; | &nbsp;&nbsp;.&nbsp; | &nbsp;&nbsp;.&nbsp; | &nbsp;&nbsp;.&nbsp; | &nbsp;&nbsp;.&nbsp; | &nbsp;&nbsp;.&nbsp; | &nbsp;&nbsp;.&nbsp; | &nbsp;&nbsp;2&nbsp; | &nbsp;&nbsp;.&nbsp; | &nbsp;&nbsp;.&nbsp; | &nbsp;&nbsp;.&nbsp; | &nbsp;&nbsp;.&nbsp; | &nbsp;&nbsp;.&nbsp; | &nbsp;&nbsp;.&nbsp; |  &nbsp;&nbsp;3&nbsp; | &nbsp;&nbsp; Screw M4 cap x 20mm |
| &nbsp;&nbsp;.&nbsp; | &nbsp;&nbsp;.&nbsp; | &nbsp;&nbsp;.&nbsp; | &nbsp;&nbsp;.&nbsp; | &nbsp;&nbsp;.&nbsp; | &nbsp;&nbsp;.&nbsp; | &nbsp;&nbsp;.&nbsp; | &nbsp;&nbsp;.&nbsp; | &nbsp;&nbsp;.&nbsp; | &nbsp;&nbsp;.&nbsp; | &nbsp;&nbsp;.&nbsp; | &nbsp;&nbsp;.&nbsp; | &nbsp;&nbsp;.&nbsp; | &nbsp;&nbsp;.&nbsp; | &nbsp;&nbsp;.&nbsp; | &nbsp;&nbsp;.&nbsp; | &nbsp;&nbsp;8&nbsp; | &nbsp;&nbsp;.&nbsp; | &nbsp;&nbsp;.&nbsp; |  &nbsp;&nbsp;8&nbsp; | &nbsp;&nbsp; Smooth rod 8mm x 30mm |
| &nbsp;&nbsp;.&nbsp; | &nbsp;&nbsp;.&nbsp; | &nbsp;&nbsp;.&nbsp; | &nbsp;&nbsp;.&nbsp; | &nbsp;&nbsp;.&nbsp; | &nbsp;&nbsp;2&nbsp; | &nbsp;&nbsp;.&nbsp; | &nbsp;&nbsp;.&nbsp; | &nbsp;&nbsp;.&nbsp; | &nbsp;&nbsp;.&nbsp; | &nbsp;&nbsp;.&nbsp; | &nbsp;&nbsp;.&nbsp; | &nbsp;&nbsp;.&nbsp; | &nbsp;&nbsp;.&nbsp; | &nbsp;&nbsp;.&nbsp; | &nbsp;&nbsp;.&nbsp; | &nbsp;&nbsp;.&nbsp; | &nbsp;&nbsp;.&nbsp; | &nbsp;&nbsp;.&nbsp; |  &nbsp;&nbsp;2&nbsp; | &nbsp;&nbsp; Smooth rod 8mm x 343mm |
| &nbsp;&nbsp;.&nbsp; | &nbsp;&nbsp;.&nbsp; | &nbsp;&nbsp;.&nbsp; | &nbsp;&nbsp;.&nbsp; | &nbsp;&nbsp;.&nbsp; | &nbsp;&nbsp;.&nbsp; | &nbsp;&nbsp;.&nbsp; | &nbsp;&nbsp;.&nbsp; | &nbsp;&nbsp;.&nbsp; | &nbsp;&nbsp;.&nbsp; | &nbsp;&nbsp;.&nbsp; | &nbsp;&nbsp;.&nbsp; | &nbsp;&nbsp;.&nbsp; | &nbsp;&nbsp;.&nbsp; | &nbsp;&nbsp;.&nbsp; | &nbsp;&nbsp;.&nbsp; | &nbsp;&nbsp;.&nbsp; | &nbsp;&nbsp;4&nbsp; | &nbsp;&nbsp;.&nbsp; |  &nbsp;&nbsp;4&nbsp; | &nbsp;&nbsp; Smooth rod 8mm x 345mm |
| &nbsp;&nbsp;.&nbsp; | &nbsp;&nbsp;.&nbsp; | &nbsp;&nbsp;.&nbsp; | &nbsp;&nbsp;.&nbsp; | &nbsp;&nbsp;.&nbsp; | &nbsp;&nbsp;.&nbsp; | &nbsp;&nbsp;.&nbsp; | &nbsp;&nbsp;.&nbsp; | &nbsp;&nbsp;4&nbsp; | &nbsp;&nbsp;.&nbsp; | &nbsp;&nbsp;.&nbsp; | &nbsp;&nbsp;.&nbsp; | &nbsp;&nbsp;.&nbsp; | &nbsp;&nbsp;.&nbsp; | &nbsp;&nbsp;.&nbsp; | &nbsp;&nbsp;.&nbsp; | &nbsp;&nbsp;.&nbsp; | &nbsp;&nbsp;.&nbsp; | &nbsp;&nbsp;.&nbsp; |  &nbsp;&nbsp;4&nbsp; | &nbsp;&nbsp; Stepper Motor Driver |
| &nbsp;&nbsp;.&nbsp; | &nbsp;&nbsp;.&nbsp; | &nbsp;&nbsp;.&nbsp; | &nbsp;&nbsp;.&nbsp; | &nbsp;&nbsp;.&nbsp; | &nbsp;&nbsp;.&nbsp; | &nbsp;&nbsp;.&nbsp; | &nbsp;&nbsp;.&nbsp; | &nbsp;&nbsp;.&nbsp; | &nbsp;&nbsp;1&nbsp; | &nbsp;&nbsp;1&nbsp; | &nbsp;&nbsp;.&nbsp; | &nbsp;&nbsp;.&nbsp; | &nbsp;&nbsp;.&nbsp; | &nbsp;&nbsp;.&nbsp; | &nbsp;&nbsp;.&nbsp; | &nbsp;&nbsp;.&nbsp; | &nbsp;&nbsp;.&nbsp; | &nbsp;&nbsp;.&nbsp; |  &nbsp;&nbsp;2&nbsp; | &nbsp;&nbsp; Stepper motor NEMA17 x 34mm |
| &nbsp;&nbsp;.&nbsp; | &nbsp;&nbsp;.&nbsp; | &nbsp;&nbsp;.&nbsp; | &nbsp;&nbsp;1&nbsp; | &nbsp;&nbsp;.&nbsp; | &nbsp;&nbsp;.&nbsp; | &nbsp;&nbsp;.&nbsp; | &nbsp;&nbsp;.&nbsp; | &nbsp;&nbsp;.&nbsp; | &nbsp;&nbsp;.&nbsp; | &nbsp;&nbsp;.&nbsp; | &nbsp;&nbsp;.&nbsp; | &nbsp;&nbsp;.&nbsp; | &nbsp;&nbsp;.&nbsp; | &nbsp;&nbsp;.&nbsp; | &nbsp;&nbsp;.&nbsp; | &nbsp;&nbsp;.&nbsp; | &nbsp;&nbsp;.&nbsp; | &nbsp;&nbsp;.&nbsp; |  &nbsp;&nbsp;1&nbsp; | &nbsp;&nbsp; Stepper motor NEMA17 x 40mm |
| &nbsp;&nbsp;.&nbsp; | &nbsp;&nbsp;.&nbsp; | &nbsp;&nbsp;.&nbsp; | &nbsp;&nbsp;.&nbsp; | &nbsp;&nbsp;.&nbsp; | &nbsp;&nbsp;.&nbsp; | &nbsp;&nbsp;.&nbsp; | &nbsp;&nbsp;.&nbsp; | &nbsp;&nbsp;1&nbsp; | &nbsp;&nbsp;.&nbsp; | &nbsp;&nbsp;.&nbsp; | &nbsp;&nbsp;.&nbsp; | &nbsp;&nbsp;.&nbsp; | &nbsp;&nbsp;.&nbsp; | &nbsp;&nbsp;.&nbsp; | &nbsp;&nbsp;.&nbsp; | &nbsp;&nbsp;.&nbsp; | &nbsp;&nbsp;.&nbsp; | &nbsp;&nbsp;.&nbsp; |  &nbsp;&nbsp;1&nbsp; | &nbsp;&nbsp; Terminal block 2 way 3.5mm |
| &nbsp;&nbsp;.&nbsp; | &nbsp;&nbsp;.&nbsp; | &nbsp;&nbsp;.&nbsp; | &nbsp;&nbsp;.&nbsp; | &nbsp;&nbsp;.&nbsp; | &nbsp;&nbsp;.&nbsp; | &nbsp;&nbsp;1&nbsp; | &nbsp;&nbsp;.&nbsp; | &nbsp;&nbsp;.&nbsp; | &nbsp;&nbsp;.&nbsp; | &nbsp;&nbsp;.&nbsp; | &nbsp;&nbsp;.&nbsp; | &nbsp;&nbsp;.&nbsp; | &nbsp;&nbsp;.&nbsp; | &nbsp;&nbsp;.&nbsp; | &nbsp;&nbsp;.&nbsp; | &nbsp;&nbsp;.&nbsp; | &nbsp;&nbsp;.&nbsp; | &nbsp;&nbsp;.&nbsp; |  &nbsp;&nbsp;1&nbsp; | &nbsp;&nbsp; Toggle switch CK7101 |
| &nbsp;&nbsp;.&nbsp; | &nbsp;&nbsp;.&nbsp; | &nbsp;&nbsp;.&nbsp; | &nbsp;&nbsp;.&nbsp; | &nbsp;&nbsp;.&nbsp; | &nbsp;&nbsp;.&nbsp; | &nbsp;&nbsp;.&nbsp; | &nbsp;&nbsp;.&nbsp; | &nbsp;&nbsp;.&nbsp; | &nbsp;&nbsp;4&nbsp; | &nbsp;&nbsp;4&nbsp; | &nbsp;&nbsp;.&nbsp; | &nbsp;&nbsp;.&nbsp; | &nbsp;&nbsp;.&nbsp; | &nbsp;&nbsp;.&nbsp; | &nbsp;&nbsp;.&nbsp; | &nbsp;&nbsp;.&nbsp; | &nbsp;&nbsp;.&nbsp; | &nbsp;&nbsp;.&nbsp; |  &nbsp;&nbsp;8&nbsp; | &nbsp;&nbsp; Washer  M3 x 7mm x 0.5mm |
| &nbsp;&nbsp;.&nbsp; | &nbsp;&nbsp;.&nbsp; | &nbsp;&nbsp;2&nbsp; | &nbsp;&nbsp;.&nbsp; | &nbsp;&nbsp;.&nbsp; | &nbsp;&nbsp;.&nbsp; | &nbsp;&nbsp;.&nbsp; | &nbsp;&nbsp;.&nbsp; | &nbsp;&nbsp;.&nbsp; | &nbsp;&nbsp;.&nbsp; | &nbsp;&nbsp;.&nbsp; | &nbsp;&nbsp;.&nbsp; | &nbsp;&nbsp;4&nbsp; | &nbsp;&nbsp;.&nbsp; | &nbsp;&nbsp;.&nbsp; | &nbsp;&nbsp;.&nbsp; | &nbsp;&nbsp;.&nbsp; | &nbsp;&nbsp;.&nbsp; | &nbsp;&nbsp;8&nbsp; |  &nbsp;&nbsp;14&nbsp; | &nbsp;&nbsp; Washer  M4 x 9mm x 0.8mm |
| &nbsp;&nbsp;.&nbsp; | &nbsp;&nbsp;.&nbsp; | &nbsp;&nbsp;.&nbsp; | &nbsp;&nbsp;.&nbsp; | &nbsp;&nbsp;.&nbsp; | &nbsp;&nbsp;.&nbsp; | &nbsp;&nbsp;.&nbsp; | &nbsp;&nbsp;.&nbsp; | &nbsp;&nbsp;.&nbsp; | &nbsp;&nbsp;4&nbsp; | &nbsp;&nbsp;4&nbsp; | &nbsp;&nbsp;.&nbsp; | &nbsp;&nbsp;.&nbsp; | &nbsp;&nbsp;.&nbsp; | &nbsp;&nbsp;.&nbsp; | &nbsp;&nbsp;.&nbsp; | &nbsp;&nbsp;.&nbsp; | &nbsp;&nbsp;.&nbsp; | &nbsp;&nbsp;.&nbsp; |  &nbsp;&nbsp;8&nbsp; | &nbsp;&nbsp; Washer star M3 x 0.5mm |
| &nbsp;&nbsp;.&nbsp; | &nbsp;&nbsp;.&nbsp; | &nbsp;&nbsp;.&nbsp; | &nbsp;&nbsp;.&nbsp; | &nbsp;&nbsp;.&nbsp; | &nbsp;&nbsp;.&nbsp; | &nbsp;&nbsp;.&nbsp; | &nbsp;&nbsp;.&nbsp; | &nbsp;&nbsp;.&nbsp; | &nbsp;&nbsp;.&nbsp; | &nbsp;&nbsp;.&nbsp; | &nbsp;&nbsp;.&nbsp; | &nbsp;&nbsp;.&nbsp; | &nbsp;&nbsp;.&nbsp; | &nbsp;&nbsp;.&nbsp; | &nbsp;&nbsp;.&nbsp; | &nbsp;&nbsp;8&nbsp; | &nbsp;&nbsp;.&nbsp; | &nbsp;&nbsp;.&nbsp; |  &nbsp;&nbsp;8&nbsp; | &nbsp;&nbsp; Ziptie 2.5mm x 100mm min length |
| &nbsp;&nbsp;.&nbsp; | &nbsp;&nbsp;1&nbsp; | &nbsp;&nbsp;.&nbsp; | &nbsp;&nbsp;.&nbsp; | &nbsp;&nbsp;.&nbsp; | &nbsp;&nbsp;.&nbsp; | &nbsp;&nbsp;.&nbsp; | &nbsp;&nbsp;.&nbsp; | &nbsp;&nbsp;.&nbsp; | &nbsp;&nbsp;.&nbsp; | &nbsp;&nbsp;.&nbsp; | &nbsp;&nbsp;.&nbsp; | &nbsp;&nbsp;.&nbsp; | &nbsp;&nbsp;.&nbsp; | &nbsp;&nbsp;.&nbsp; | &nbsp;&nbsp;.&nbsp; | &nbsp;&nbsp;.&nbsp; | &nbsp;&nbsp;.&nbsp; | &nbsp;&nbsp;.&nbsp; |  &nbsp;&nbsp;1&nbsp; | &nbsp;&nbsp; Ziptie 2.5mm x 100mm min length |
| &nbsp;&nbsp;1&nbsp; | &nbsp;&nbsp;.&nbsp; | &nbsp;&nbsp;.&nbsp; | &nbsp;&nbsp;.&nbsp; | &nbsp;&nbsp;.&nbsp; | &nbsp;&nbsp;.&nbsp; | &nbsp;&nbsp;.&nbsp; | &nbsp;&nbsp;.&nbsp; | &nbsp;&nbsp;.&nbsp; | &nbsp;&nbsp;.&nbsp; | &nbsp;&nbsp;.&nbsp; | &nbsp;&nbsp;.&nbsp; | &nbsp;&nbsp;.&nbsp; | &nbsp;&nbsp;.&nbsp; | &nbsp;&nbsp;.&nbsp; | &nbsp;&nbsp;.&nbsp; | &nbsp;&nbsp;.&nbsp; | &nbsp;&nbsp;.&nbsp; | &nbsp;&nbsp;.&nbsp; |  &nbsp;&nbsp;1&nbsp; | &nbsp;&nbsp;laser module |
| &nbsp;&nbsp;2&nbsp; | &nbsp;&nbsp;13&nbsp; | &nbsp;&nbsp;6&nbsp; | &nbsp;&nbsp;4&nbsp; | &nbsp;&nbsp;4&nbsp; | &nbsp;&nbsp;2&nbsp; | &nbsp;&nbsp;2&nbsp; | &nbsp;&nbsp;10&nbsp; | &nbsp;&nbsp;18&nbsp; | &nbsp;&nbsp;18&nbsp; | &nbsp;&nbsp;18&nbsp; | &nbsp;&nbsp;1&nbsp; | &nbsp;&nbsp;18&nbsp; | &nbsp;&nbsp;1&nbsp; | &nbsp;&nbsp;24&nbsp; | &nbsp;&nbsp;36&nbsp; | &nbsp;&nbsp;32&nbsp; | &nbsp;&nbsp;6&nbsp; | &nbsp;&nbsp;32&nbsp; | &nbsp;&nbsp;247&nbsp; | &nbsp;&nbsp;Total vitamins count |
|  |  |  |  |  |  |  |  |  |  |  |  |  |  |  |  |  |  |  | | **3D printed parts** |
| &nbsp;&nbsp;.&nbsp; | &nbsp;&nbsp;.&nbsp; | &nbsp;&nbsp;.&nbsp; | &nbsp;&nbsp;.&nbsp; | &nbsp;&nbsp;.&nbsp; | &nbsp;&nbsp;.&nbsp; | &nbsp;&nbsp;.&nbsp; | &nbsp;&nbsp;1&nbsp; | &nbsp;&nbsp;.&nbsp; | &nbsp;&nbsp;.&nbsp; | &nbsp;&nbsp;.&nbsp; | &nbsp;&nbsp;.&nbsp; | &nbsp;&nbsp;.&nbsp; | &nbsp;&nbsp;.&nbsp; | &nbsp;&nbsp;.&nbsp; | &nbsp;&nbsp;.&nbsp; | &nbsp;&nbsp;.&nbsp; | &nbsp;&nbsp;.&nbsp; | &nbsp;&nbsp;.&nbsp; |  &nbsp;&nbsp;1&nbsp; | &nbsp;&nbsp;ele_box_base.stl |
| &nbsp;&nbsp;.&nbsp; | &nbsp;&nbsp;.&nbsp; | &nbsp;&nbsp;.&nbsp; | &nbsp;&nbsp;.&nbsp; | &nbsp;&nbsp;.&nbsp; | &nbsp;&nbsp;.&nbsp; | &nbsp;&nbsp;1&nbsp; | &nbsp;&nbsp;.&nbsp; | &nbsp;&nbsp;.&nbsp; | &nbsp;&nbsp;.&nbsp; | &nbsp;&nbsp;.&nbsp; | &nbsp;&nbsp;.&nbsp; | &nbsp;&nbsp;.&nbsp; | &nbsp;&nbsp;.&nbsp; | &nbsp;&nbsp;.&nbsp; | &nbsp;&nbsp;.&nbsp; | &nbsp;&nbsp;.&nbsp; | &nbsp;&nbsp;.&nbsp; | &nbsp;&nbsp;.&nbsp; |  &nbsp;&nbsp;1&nbsp; | &nbsp;&nbsp;ele_box_top.stl |
| &nbsp;&nbsp;.&nbsp; | &nbsp;&nbsp;.&nbsp; | &nbsp;&nbsp;.&nbsp; | &nbsp;&nbsp;.&nbsp; | &nbsp;&nbsp;.&nbsp; | &nbsp;&nbsp;.&nbsp; | &nbsp;&nbsp;.&nbsp; | &nbsp;&nbsp;.&nbsp; | &nbsp;&nbsp;.&nbsp; | &nbsp;&nbsp;.&nbsp; | &nbsp;&nbsp;.&nbsp; | &nbsp;&nbsp;1&nbsp; | &nbsp;&nbsp;.&nbsp; | &nbsp;&nbsp;.&nbsp; | &nbsp;&nbsp;.&nbsp; | &nbsp;&nbsp;.&nbsp; | &nbsp;&nbsp;.&nbsp; | &nbsp;&nbsp;.&nbsp; | &nbsp;&nbsp;.&nbsp; |  &nbsp;&nbsp;1&nbsp; | &nbsp;&nbsp;ele_bracket.stl |
| &nbsp;&nbsp;.&nbsp; | &nbsp;&nbsp;1&nbsp; | &nbsp;&nbsp;.&nbsp; | &nbsp;&nbsp;.&nbsp; | &nbsp;&nbsp;.&nbsp; | &nbsp;&nbsp;.&nbsp; | &nbsp;&nbsp;.&nbsp; | &nbsp;&nbsp;.&nbsp; | &nbsp;&nbsp;.&nbsp; | &nbsp;&nbsp;.&nbsp; | &nbsp;&nbsp;.&nbsp; | &nbsp;&nbsp;.&nbsp; | &nbsp;&nbsp;.&nbsp; | &nbsp;&nbsp;.&nbsp; | &nbsp;&nbsp;.&nbsp; | &nbsp;&nbsp;.&nbsp; | &nbsp;&nbsp;.&nbsp; | &nbsp;&nbsp;.&nbsp; | &nbsp;&nbsp;.&nbsp; |  &nbsp;&nbsp;1&nbsp; | &nbsp;&nbsp;laser_wire_holder.stl |
| &nbsp;&nbsp;.&nbsp; | &nbsp;&nbsp;1&nbsp; | &nbsp;&nbsp;.&nbsp; | &nbsp;&nbsp;.&nbsp; | &nbsp;&nbsp;.&nbsp; | &nbsp;&nbsp;.&nbsp; | &nbsp;&nbsp;.&nbsp; | &nbsp;&nbsp;.&nbsp; | &nbsp;&nbsp;.&nbsp; | &nbsp;&nbsp;.&nbsp; | &nbsp;&nbsp;.&nbsp; | &nbsp;&nbsp;.&nbsp; | &nbsp;&nbsp;.&nbsp; | &nbsp;&nbsp;.&nbsp; | &nbsp;&nbsp;.&nbsp; | &nbsp;&nbsp;.&nbsp; | &nbsp;&nbsp;.&nbsp; | &nbsp;&nbsp;.&nbsp; | &nbsp;&nbsp;.&nbsp; |  &nbsp;&nbsp;1&nbsp; | &nbsp;&nbsp;x_carriage_back.stl |
| &nbsp;&nbsp;.&nbsp; | &nbsp;&nbsp;1&nbsp; | &nbsp;&nbsp;.&nbsp; | &nbsp;&nbsp;.&nbsp; | &nbsp;&nbsp;.&nbsp; | &nbsp;&nbsp;.&nbsp; | &nbsp;&nbsp;.&nbsp; | &nbsp;&nbsp;.&nbsp; | &nbsp;&nbsp;.&nbsp; | &nbsp;&nbsp;.&nbsp; | &nbsp;&nbsp;.&nbsp; | &nbsp;&nbsp;.&nbsp; | &nbsp;&nbsp;.&nbsp; | &nbsp;&nbsp;.&nbsp; | &nbsp;&nbsp;.&nbsp; | &nbsp;&nbsp;.&nbsp; | &nbsp;&nbsp;.&nbsp; | &nbsp;&nbsp;.&nbsp; | &nbsp;&nbsp;.&nbsp; |  &nbsp;&nbsp;1&nbsp; | &nbsp;&nbsp;x_carriage_front.stl |
| &nbsp;&nbsp;.&nbsp; | &nbsp;&nbsp;.&nbsp; | &nbsp;&nbsp;1&nbsp; | &nbsp;&nbsp;.&nbsp; | &nbsp;&nbsp;.&nbsp; | &nbsp;&nbsp;.&nbsp; | &nbsp;&nbsp;.&nbsp; | &nbsp;&nbsp;.&nbsp; | &nbsp;&nbsp;.&nbsp; | &nbsp;&nbsp;.&nbsp; | &nbsp;&nbsp;.&nbsp; | &nbsp;&nbsp;.&nbsp; | &nbsp;&nbsp;.&nbsp; | &nbsp;&nbsp;.&nbsp; | &nbsp;&nbsp;.&nbsp; | &nbsp;&nbsp;.&nbsp; | &nbsp;&nbsp;.&nbsp; | &nbsp;&nbsp;.&nbsp; | &nbsp;&nbsp;.&nbsp; |  &nbsp;&nbsp;1&nbsp; | &nbsp;&nbsp;x_idler.stl |
| &nbsp;&nbsp;.&nbsp; | &nbsp;&nbsp;.&nbsp; | &nbsp;&nbsp;.&nbsp; | &nbsp;&nbsp;.&nbsp; | &nbsp;&nbsp;1&nbsp; | &nbsp;&nbsp;.&nbsp; | &nbsp;&nbsp;.&nbsp; | &nbsp;&nbsp;.&nbsp; | &nbsp;&nbsp;.&nbsp; | &nbsp;&nbsp;.&nbsp; | &nbsp;&nbsp;.&nbsp; | &nbsp;&nbsp;.&nbsp; | &nbsp;&nbsp;.&nbsp; | &nbsp;&nbsp;.&nbsp; | &nbsp;&nbsp;.&nbsp; | &nbsp;&nbsp;.&nbsp; | &nbsp;&nbsp;.&nbsp; | &nbsp;&nbsp;.&nbsp; | &nbsp;&nbsp;.&nbsp; |  &nbsp;&nbsp;1&nbsp; | &nbsp;&nbsp;x_motor_holder_mount.stl |
| &nbsp;&nbsp;.&nbsp; | &nbsp;&nbsp;.&nbsp; | &nbsp;&nbsp;.&nbsp; | &nbsp;&nbsp;.&nbsp; | &nbsp;&nbsp;.&nbsp; | &nbsp;&nbsp;.&nbsp; | &nbsp;&nbsp;.&nbsp; | &nbsp;&nbsp;.&nbsp; | &nbsp;&nbsp;.&nbsp; | &nbsp;&nbsp;.&nbsp; | &nbsp;&nbsp;.&nbsp; | &nbsp;&nbsp;.&nbsp; | &nbsp;&nbsp;.&nbsp; | &nbsp;&nbsp;.&nbsp; | &nbsp;&nbsp;.&nbsp; | &nbsp;&nbsp;.&nbsp; | &nbsp;&nbsp;8&nbsp; | &nbsp;&nbsp;.&nbsp; | &nbsp;&nbsp;.&nbsp; |  &nbsp;&nbsp;8&nbsp; | &nbsp;&nbsp;y_axis_holder.stl |
| &nbsp;&nbsp;.&nbsp; | &nbsp;&nbsp;.&nbsp; | &nbsp;&nbsp;.&nbsp; | &nbsp;&nbsp;.&nbsp; | &nbsp;&nbsp;.&nbsp; | &nbsp;&nbsp;.&nbsp; | &nbsp;&nbsp;.&nbsp; | &nbsp;&nbsp;.&nbsp; | &nbsp;&nbsp;.&nbsp; | &nbsp;&nbsp;.&nbsp; | &nbsp;&nbsp;.&nbsp; | &nbsp;&nbsp;.&nbsp; | &nbsp;&nbsp;.&nbsp; | &nbsp;&nbsp;.&nbsp; | &nbsp;&nbsp;2&nbsp; | &nbsp;&nbsp;.&nbsp; | &nbsp;&nbsp;.&nbsp; | &nbsp;&nbsp;.&nbsp; | &nbsp;&nbsp;.&nbsp; |  &nbsp;&nbsp;2&nbsp; | &nbsp;&nbsp;y_carriage_base.stl |
| &nbsp;&nbsp;.&nbsp; | &nbsp;&nbsp;.&nbsp; | &nbsp;&nbsp;.&nbsp; | &nbsp;&nbsp;.&nbsp; | &nbsp;&nbsp;.&nbsp; | &nbsp;&nbsp;.&nbsp; | &nbsp;&nbsp;.&nbsp; | &nbsp;&nbsp;.&nbsp; | &nbsp;&nbsp;.&nbsp; | &nbsp;&nbsp;.&nbsp; | &nbsp;&nbsp;.&nbsp; | &nbsp;&nbsp;.&nbsp; | &nbsp;&nbsp;.&nbsp; | &nbsp;&nbsp;.&nbsp; | &nbsp;&nbsp;.&nbsp; | &nbsp;&nbsp;.&nbsp; | &nbsp;&nbsp;.&nbsp; | &nbsp;&nbsp;.&nbsp; | &nbsp;&nbsp;2&nbsp; |  &nbsp;&nbsp;2&nbsp; | &nbsp;&nbsp;y_carriage_belt_clamp.stl |
| &nbsp;&nbsp;.&nbsp; | &nbsp;&nbsp;.&nbsp; | &nbsp;&nbsp;.&nbsp; | &nbsp;&nbsp;.&nbsp; | &nbsp;&nbsp;.&nbsp; | &nbsp;&nbsp;.&nbsp; | &nbsp;&nbsp;.&nbsp; | &nbsp;&nbsp;.&nbsp; | &nbsp;&nbsp;.&nbsp; | &nbsp;&nbsp;.&nbsp; | &nbsp;&nbsp;.&nbsp; | &nbsp;&nbsp;.&nbsp; | &nbsp;&nbsp;2&nbsp; | &nbsp;&nbsp;.&nbsp; | &nbsp;&nbsp;.&nbsp; | &nbsp;&nbsp;.&nbsp; | &nbsp;&nbsp;.&nbsp; | &nbsp;&nbsp;.&nbsp; | &nbsp;&nbsp;.&nbsp; |  &nbsp;&nbsp;2&nbsp; | &nbsp;&nbsp;y_idler.stl |
| &nbsp;&nbsp;.&nbsp; | &nbsp;&nbsp;.&nbsp; | &nbsp;&nbsp;.&nbsp; | &nbsp;&nbsp;.&nbsp; | &nbsp;&nbsp;.&nbsp; | &nbsp;&nbsp;.&nbsp; | &nbsp;&nbsp;.&nbsp; | &nbsp;&nbsp;.&nbsp; | &nbsp;&nbsp;.&nbsp; | &nbsp;&nbsp;.&nbsp; | &nbsp;&nbsp;.&nbsp; | &nbsp;&nbsp;.&nbsp; | &nbsp;&nbsp;.&nbsp; | &nbsp;&nbsp;.&nbsp; | &nbsp;&nbsp;.&nbsp; | &nbsp;&nbsp;4&nbsp; | &nbsp;&nbsp;.&nbsp; | &nbsp;&nbsp;.&nbsp; | &nbsp;&nbsp;.&nbsp; |  &nbsp;&nbsp;4&nbsp; | &nbsp;&nbsp;y_limit_switch.stl |
| &nbsp;&nbsp;.&nbsp; | &nbsp;&nbsp;.&nbsp; | &nbsp;&nbsp;.&nbsp; | &nbsp;&nbsp;.&nbsp; | &nbsp;&nbsp;.&nbsp; | &nbsp;&nbsp;.&nbsp; | &nbsp;&nbsp;.&nbsp; | &nbsp;&nbsp;.&nbsp; | &nbsp;&nbsp;.&nbsp; | &nbsp;&nbsp;.&nbsp; | &nbsp;&nbsp;.&nbsp; | &nbsp;&nbsp;.&nbsp; | &nbsp;&nbsp;.&nbsp; | &nbsp;&nbsp;.&nbsp; | &nbsp;&nbsp;2&nbsp; | &nbsp;&nbsp;.&nbsp; | &nbsp;&nbsp;.&nbsp; | &nbsp;&nbsp;.&nbsp; | &nbsp;&nbsp;.&nbsp; |  &nbsp;&nbsp;2&nbsp; | &nbsp;&nbsp;y_limit_switch_hitter.stl |
| &nbsp;&nbsp;.&nbsp; | &nbsp;&nbsp;.&nbsp; | &nbsp;&nbsp;.&nbsp; | &nbsp;&nbsp;.&nbsp; | &nbsp;&nbsp;.&nbsp; | &nbsp;&nbsp;.&nbsp; | &nbsp;&nbsp;.&nbsp; | &nbsp;&nbsp;.&nbsp; | &nbsp;&nbsp;.&nbsp; | &nbsp;&nbsp;.&nbsp; | &nbsp;&nbsp;1&nbsp; | &nbsp;&nbsp;.&nbsp; | &nbsp;&nbsp;.&nbsp; | &nbsp;&nbsp;.&nbsp; | &nbsp;&nbsp;.&nbsp; | &nbsp;&nbsp;.&nbsp; | &nbsp;&nbsp;.&nbsp; | &nbsp;&nbsp;.&nbsp; | &nbsp;&nbsp;.&nbsp; |  &nbsp;&nbsp;1&nbsp; | &nbsp;&nbsp;y_motor_left_mount.stl |
| &nbsp;&nbsp;.&nbsp; | &nbsp;&nbsp;.&nbsp; | &nbsp;&nbsp;.&nbsp; | &nbsp;&nbsp;.&nbsp; | &nbsp;&nbsp;.&nbsp; | &nbsp;&nbsp;.&nbsp; | &nbsp;&nbsp;.&nbsp; | &nbsp;&nbsp;.&nbsp; | &nbsp;&nbsp;.&nbsp; | &nbsp;&nbsp;1&nbsp; | &nbsp;&nbsp;.&nbsp; | &nbsp;&nbsp;.&nbsp; | &nbsp;&nbsp;.&nbsp; | &nbsp;&nbsp;.&nbsp; | &nbsp;&nbsp;.&nbsp; | &nbsp;&nbsp;.&nbsp; | &nbsp;&nbsp;.&nbsp; | &nbsp;&nbsp;.&nbsp; | &nbsp;&nbsp;.&nbsp; |  &nbsp;&nbsp;1&nbsp; | &nbsp;&nbsp;y_motor_right_mount.stl |
| &nbsp;&nbsp;.&nbsp; | &nbsp;&nbsp;3&nbsp; | &nbsp;&nbsp;1&nbsp; | &nbsp;&nbsp;.&nbsp; | &nbsp;&nbsp;1&nbsp; | &nbsp;&nbsp;.&nbsp; | &nbsp;&nbsp;1&nbsp; | &nbsp;&nbsp;1&nbsp; | &nbsp;&nbsp;.&nbsp; | &nbsp;&nbsp;1&nbsp; | &nbsp;&nbsp;1&nbsp; | &nbsp;&nbsp;1&nbsp; | &nbsp;&nbsp;2&nbsp; | &nbsp;&nbsp;.&nbsp; | &nbsp;&nbsp;4&nbsp; | &nbsp;&nbsp;4&nbsp; | &nbsp;&nbsp;8&nbsp; | &nbsp;&nbsp;.&nbsp; | &nbsp;&nbsp;2&nbsp; | &nbsp;&nbsp;30&nbsp; | &nbsp;&nbsp;Total 3D printed parts count |

## Laser Module Assembly
### Vitamins
|Qty|Description|
|---:|:---|
|1| Fan 40mm x 11mm|

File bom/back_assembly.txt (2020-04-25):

back_assembly:
Vitamins:
  1 Extrusion E3030 x 445mm

Printed:
  1 ele_bracket.stl

Assemblies:
  1 electronics_assembly
  1 y_motor_left_assembly
  1 y_motor_right_assembly

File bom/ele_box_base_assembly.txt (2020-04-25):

ele_box_base_assembly:
Vitamins:
  4 Nut M2 x 1.6mm 
  3 Nut M3 x 2.4mm 
  3 Nut M3nS 5.5 x 1.8mm 

Printed:
  1 ele_box_base.stl

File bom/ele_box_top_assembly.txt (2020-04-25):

ele_box_top_assembly:
Vitamins:
  1 LED 5 mm red
  1 Toggle switch CK7101

Printed:
  1 ele_box_top.stl

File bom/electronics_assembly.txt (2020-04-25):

electronics_assembly:
Vitamins:
  1 Terminal block 2 way 3.5mm
  1 Arduino Uno R3
  4 Stepper Motor Driver
  1 Perfboard 80 x 20mm
  8 Pin socket 8 x 1
  3 Screw M3 pan x  8mm

Assemblies:
  1 ele_box_base_assembly
  1 ele_box_top_assembly

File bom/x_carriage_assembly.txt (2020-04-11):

x_carriage_assembly:
Vitamins:
  2 Linear bearing LM8UU
  2 Nut M3 x 2.4mm 
  1 Nut M3nS 5.5 x 1.8mm 
  2 Screw M3 cap x 12mm
  1 Screw M3 cap x 20mm
  3 Screw M3 pan x 12mm
  1 Screw M3 pan x  5mm
  1 Ziptie 2.5mm x 100mm min length

Printed:
  1 laser_wire_holder.stl
  1 x_carriage_back.stl
  1 x_carriage_front.stl

Assemblies:
  1 laser_module_assembly

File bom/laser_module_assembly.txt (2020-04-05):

laser_module_assembly:
Vitamins:
  1 Fan 40mm x 11mm
  1 laser module

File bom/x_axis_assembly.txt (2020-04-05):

x_axis_assembly:
Vitamins:
  2 Smooth rod 8mm x 343mm

Assemblies:
  1 x_carriage_assembly
  1 x_idler_assembly
  1 x_motor_holder_assembly

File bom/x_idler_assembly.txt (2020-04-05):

x_idler_assembly:
Vitamins:
  1 Microswitch SS-01 or SS-5GL
  1 Nut M4 x 3.2mm 
  1 Pulley GT2 idler 20 teeth
  1 Screw M4 cap x 20mm
  2 Washer  M4 x 9mm x 0.8mm

Printed:
  1 x_idler.stl

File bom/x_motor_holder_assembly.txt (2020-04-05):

x_motor_holder_assembly:
Vitamins:
  1 Microswitch SS-01 or SS-5GL
  3 Screw M3 cap x  8mm

Printed:
  1 x_motor_holder_mount.stl

Assemblies:
  1 x_motor_and_pulley_assembly

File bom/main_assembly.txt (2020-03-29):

main_assembly:
Vitamins:
  2 Belt GT2 x 6mm x 814mm
  4 Extrusion corner bracket 20
  2 Screw M3 pan x  8mm
  8 Screw M4 cap x  8mm
  8 Nut M4 sliding T
  8 Washer  M4 x 9mm x 0.8mm

Printed:
  2 y_carriage_belt_clamp.stl

Assemblies:
  1 back_assembly
  1 front_assembly
  1 x_axis_assembly
  2 y_axis_assemblies

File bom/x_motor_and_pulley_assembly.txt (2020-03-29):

x_motor_and_pulley_assembly:
Vitamins:
  1 Stepper motor NEMA17 x 40mm
  1 Pulley GT2OB 20 teeth
  2 Screw M3 grub x  6mm

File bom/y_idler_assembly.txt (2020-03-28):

y_idler_assemblies:
Vitamins:
  2 Nut M4 x 3.2mm 
  2 Pulley GT2 idler 20 teeth
  4 Screw M4 cap x 10mm
  2 Screw M4 cap x 20mm
  4 Nut M4 sliding T
  4 Washer  M4 x 9mm x 0.8mm

Printed:
  2 y_idler.stl

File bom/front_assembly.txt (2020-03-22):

front_assembly:
Vitamins:
  1 Extrusion E3030 x 445mm

Assemblies:
  2 y_idler_assemblies

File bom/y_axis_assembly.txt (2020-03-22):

y_axis_assemblies:
Vitamins:
  2 Extrusion E3060 x 345mm
  4 Smooth rod 8mm x 345mm

Assemblies:
  8 y_axis_holder_assemblies
  2 y_carriage_base_assemblies
  4 y_limit_switch_assemblies

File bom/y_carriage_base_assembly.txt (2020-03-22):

y_carriage_base_assemblies:
Vitamins:
  6 Linear bearing LM8UU
  2 Nut M3 x 2.4mm 
 12 Nut M3nS 5.5 x 1.8mm 
  4 Screw M3 cap x  6mm

Printed:
  2 y_carriage_base.stl
  2 y_limit_switch_hitter.stl

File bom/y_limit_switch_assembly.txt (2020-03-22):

y_limit_switch_assemblies:
Vitamins:
  4 Microswitch SS-01 or SS-5GL
  8 Nut M2 x 1.6mm 
  8 Screw M2 cap x 10mm
  8 Screw M4 cap x  8mm
  8 Nut M4 hammer

Printed:
  4 y_limit_switch.stl

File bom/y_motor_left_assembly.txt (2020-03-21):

y_motor_left_assembly:
Vitamins:
  1 Stepper motor NEMA17 x 34mm
  1 Pulley GT2OB 20 teeth
  4 Screw M3 cap x  8mm
  2 Screw M4 cap x 10mm
  2 Nut M4 sliding T
  4 Washer star M3 x 0.5mm
  4 Washer  M3 x 7mm x 0.5mm

Printed:
  1 y_motor_left_mount.stl

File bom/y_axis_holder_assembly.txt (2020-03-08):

y_axis_holder_assemblies:
Vitamins:
  8 Smooth rod 8mm x 30mm
  8 Screw M4 cap x 10mm
  8 Nut M4 sliding T
  8 Ziptie 2.5mm x 100mm min length

Printed:
  8 y_axis_holder.stl

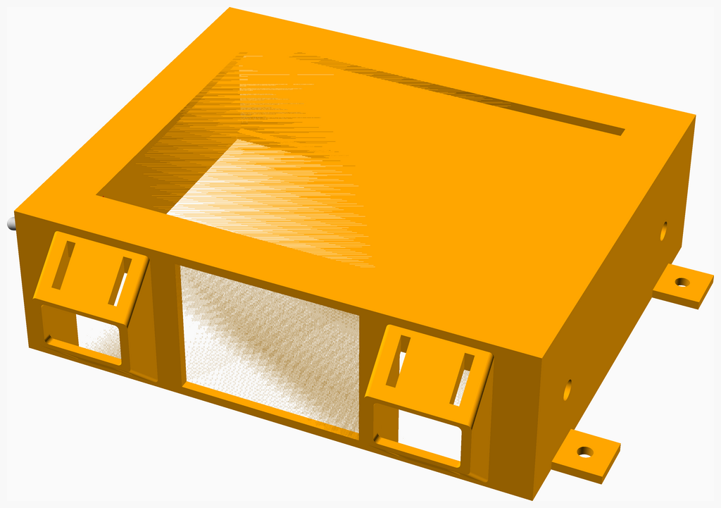
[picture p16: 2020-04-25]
assemblies/ele_box_top_assembled.png

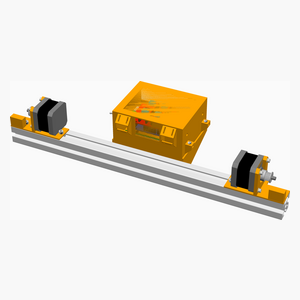
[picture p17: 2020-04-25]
assemblies/back_assembly_tn.png

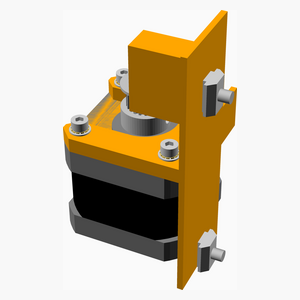
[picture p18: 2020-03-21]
assemblies/y_motor_right_assembled_tn.png

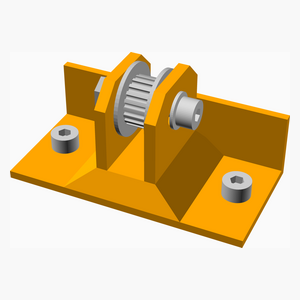
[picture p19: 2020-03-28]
assemblies/y_idler_assembled_tn.png

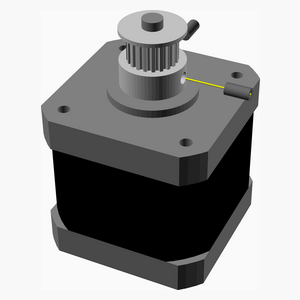
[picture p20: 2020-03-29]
assemblies/x_motor_and_pulley_assembly_tn.png

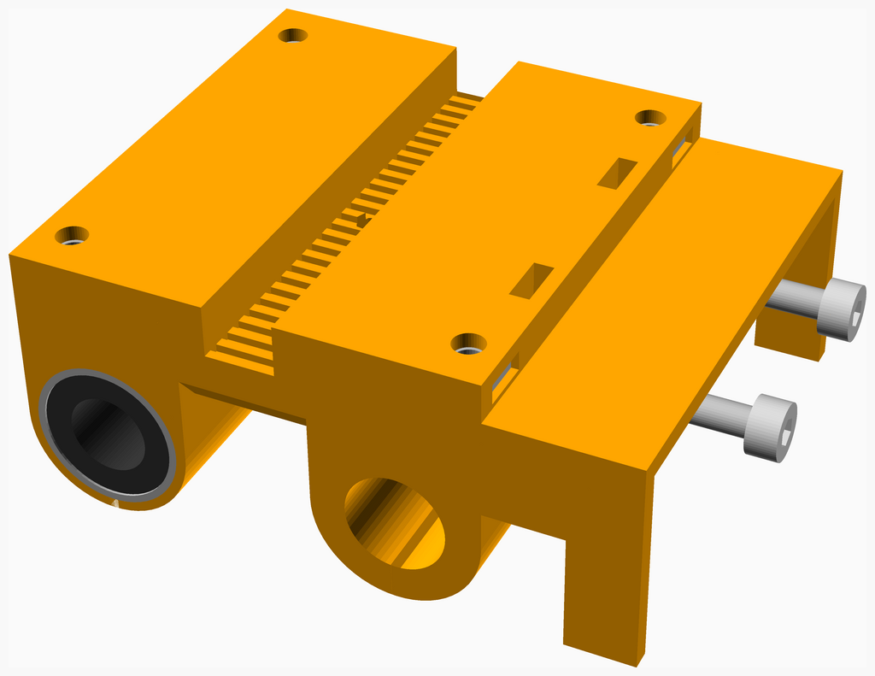
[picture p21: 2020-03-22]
assemblies/y_carriage_base_assembly.png

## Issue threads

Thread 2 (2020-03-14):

remove frame_assembly, make the assembly instructions meaningful

FLamparski, 2020-03-14:
Assembling the frame should actually be the step after all the frame-mounted parts are attached. Bigger assemblies, such as the y-axis rods on their extrusions, should be factored out for more logical assembly instructions.

Closed 2020-03-22.

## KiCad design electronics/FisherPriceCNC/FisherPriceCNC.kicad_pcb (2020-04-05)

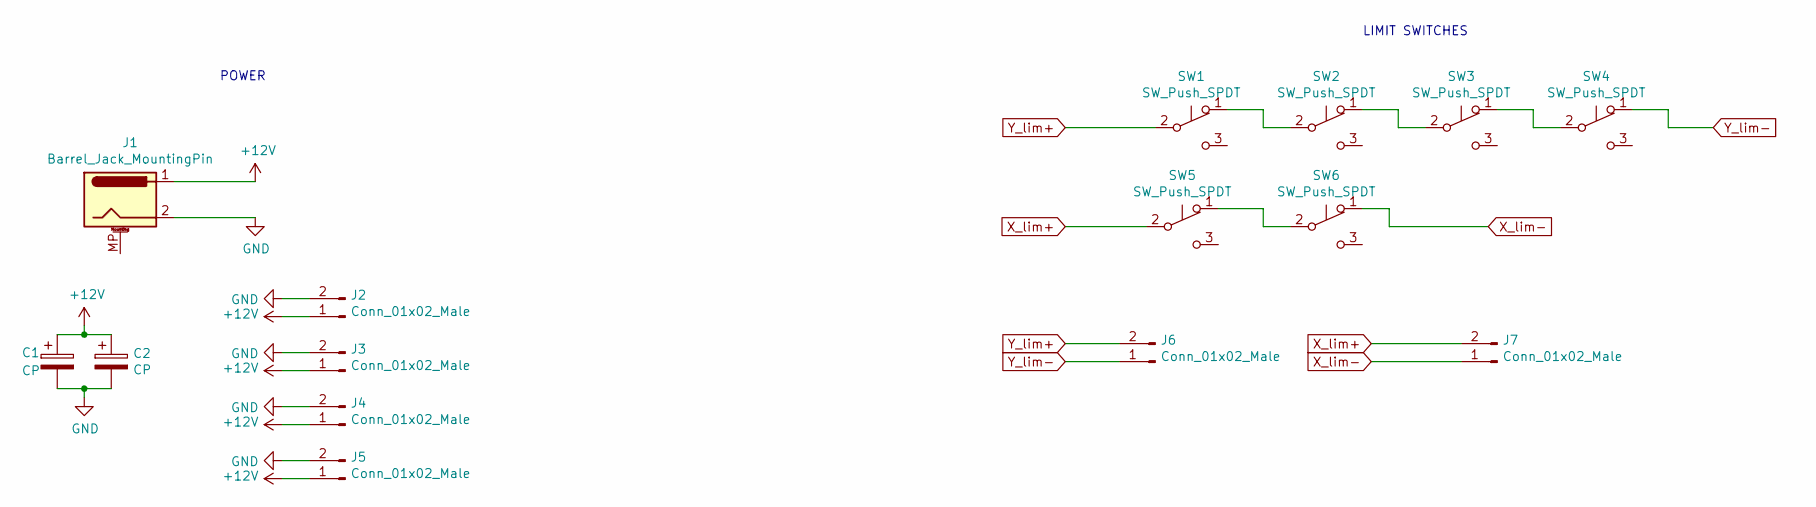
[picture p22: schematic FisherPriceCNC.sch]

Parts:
C1, C2: CP; CP_Radial_D5.0mm_P2.50mm
J1: Barrel_Jack_MountingPin; BarrelJack_Horizontal
J2, J3, J4, J5, J6, J7: Conn_01x02_Male; PinHeader_1x02_P2.54mm_Vertical
SW1, SW2, SW3, SW4, SW5, SW6: SW_Push_SPDT; PinHeader_1x02_P2.54mm_Vertical

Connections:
+12V: C1.1, C2.1, J1.1, J2.1, J3.1, J4.1, J5.1
GND: C1.2, C2.2, J1.2, J2.2, J3.2, J4.2, J5.2
unnamed: SW1.1 (A), SW2.2 (B)
unnamed: SW2.1 (A), SW3.2 (B)
unnamed: SW3.1 (A), SW4.2 (B)
unnamed: SW5.1 (A), SW6.2 (B)
X_lim+: J7.2, SW5.2 (B)
X_lim-: J7.1, SW6.1 (A)
Y_lim+: J6.2, SW1.2 (B)
Y_lim-: J6.1, SW4.1 (A)

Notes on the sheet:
POWER
LIMIT SWITCHES

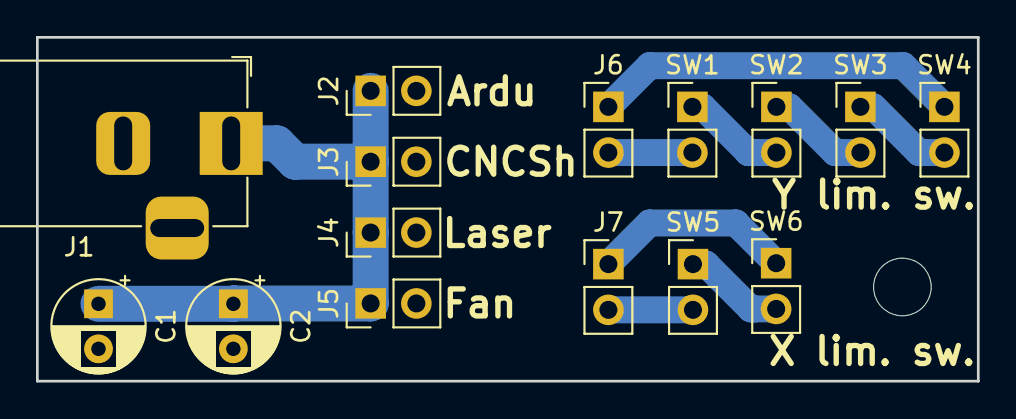
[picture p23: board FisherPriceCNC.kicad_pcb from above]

Board: 2 copper layers, 52.3 x 19.1 mm, 15 parts (0 on the bottom side), 10 nets.

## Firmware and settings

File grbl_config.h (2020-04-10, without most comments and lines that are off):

#define config_h
#include "grbl.h" // For Arduino IDE compatibility.
#define DEFAULTS_GENERIC
#define CPU_MAP_ATMEGA328P // Arduino Uno CPU
#define BAUD_RATE 115200
#define CMD_RESET 0x18 // ctrl-x.
#define CMD_STATUS_REPORT '?'
#define CMD_CYCLE_START '~'
#define CMD_FEED_HOLD '!'
#define CMD_SAFETY_DOOR 0x84
#define CMD_JOG_CANCEL  0x85
#define CMD_DEBUG_REPORT 0x86 // Only when DEBUG enabled, sends debug report in '{}' braces.
#define CMD_FEED_OVR_RESET 0x90         // Restores feed override value to 100%.
#define CMD_FEED_OVR_COARSE_PLUS 0x91
#define CMD_FEED_OVR_COARSE_MINUS 0x92
#define CMD_FEED_OVR_FINE_PLUS  0x93
#define CMD_FEED_OVR_FINE_MINUS  0x94
#define CMD_RAPID_OVR_RESET 0x95        // Restores rapid override value to 100%.
#define CMD_RAPID_OVR_MEDIUM 0x96
#define CMD_RAPID_OVR_LOW 0x97
#define CMD_SPINDLE_OVR_RESET 0x99      // Restores spindle override value to 100%.
#define CMD_SPINDLE_OVR_COARSE_PLUS 0x9A
#define CMD_SPINDLE_OVR_COARSE_MINUS 0x9B
#define CMD_SPINDLE_OVR_FINE_PLUS 0x9C
#define CMD_SPINDLE_OVR_FINE_MINUS 0x9D
#define CMD_SPINDLE_OVR_STOP 0x9E
#define CMD_COOLANT_FLOOD_OVR_TOGGLE 0xA0
#define CMD_COOLANT_MIST_OVR_TOGGLE 0xA1
#define HOMING_INIT_LOCK // Comment to disable
#define HOMING_CYCLE_0 ((1<<X_AXIS)|(1<<Y_AXIS))  // NOT COMPATIBLE WITH COREXY: Homes both X-Y in one cycle.
#define N_HOMING_LOCATE_CYCLE 1 // Integer (1-128)
#define N_STARTUP_LINE 2 // Integer (1-2)
#define N_DECIMAL_COORDVALUE_INCH 4 // Coordinate or position value in inches
#define N_DECIMAL_COORDVALUE_MM   3 // Coordinate or position value in mm
#define N_DECIMAL_RATEVALUE_INCH  1 // Rate or velocity value in in/min
#define N_DECIMAL_RATEVALUE_MM    0 // Rate or velocity value in mm/min
#define N_DECIMAL_SETTINGVALUE    3 // Decimals for floating point setting values
#define N_DECIMAL_RPMVALUE        0 // RPM value in rotations per min.
#define MESSAGE_PROBE_COORDINATES // Enabled by default. Comment to disable.
#define SAFETY_DOOR_SPINDLE_DELAY 4.0 // Float (seconds)
#define SAFETY_DOOR_COOLANT_DELAY 1.0 // Float (seconds)
#define CHECK_LIMITS_AT_INIT
#define DEFAULT_FEED_OVERRIDE           100 // 100%. Don't change this value.
#define MAX_FEED_RATE_OVERRIDE          200 // Percent of programmed feed rate (100-255). Usually 120% or 200%
#define MIN_FEED_RATE_OVERRIDE           10 // Percent of programmed feed rate (1-100). Usually 50% or 1%
#define FEED_OVERRIDE_COARSE_INCREMENT   10 // (1-99). Usually 10%.
#define FEED_OVERRIDE_FINE_INCREMENT      1 // (1-99). Usually 1%.
#define DEFAULT_RAPID_OVERRIDE  100 // 100%. Don't change this value.
#define RAPID_OVERRIDE_MEDIUM    50 // Percent of rapid (1-99). Usually 50%.
#define RAPID_OVERRIDE_LOW       25 // Percent of rapid (1-99). Usually 25%.
#define DEFAULT_SPINDLE_SPEED_OVERRIDE    100 // 100%. Don't change this value.
#define MAX_SPINDLE_SPEED_OVERRIDE        200 // Percent of programmed spindle speed (100-255). Usually 200%.
#define MIN_SPINDLE_SPEED_OVERRIDE         10 // Percent of programmed spindle speed (1-100). Usually 10%.
#define SPINDLE_OVERRIDE_COARSE_INCREMENT  10 // (1-99). Usually 10%.
#define SPINDLE_OVERRIDE_FINE_INCREMENT     1 // (1-99). Usually 1%.
#define RESTORE_OVERRIDES_AFTER_PROGRAM_END // Default enabled. Comment to disable.
#define REPORT_FIELD_BUFFER_STATE // Default enabled. Comment to disable.
#define REPORT_FIELD_PIN_STATE // Default enabled. Comment to disable.
#define REPORT_FIELD_CURRENT_FEED_SPEED // Default enabled. Comment to disable.
#define REPORT_FIELD_WORK_COORD_OFFSET // Default enabled. Comment to disable.
#define REPORT_FIELD_OVERRIDES // Default enabled. Comment to disable.
#define REPORT_FIELD_LINE_NUMBERS // Default enabled. Comment to disable.
#define REPORT_OVR_REFRESH_BUSY_COUNT 20  // (1-255)
#define REPORT_OVR_REFRESH_IDLE_COUNT 10  // (1-255) Must be less than or equal to the busy count
#define REPORT_WCO_REFRESH_BUSY_COUNT 30  // (2-255)
#define REPORT_WCO_REFRESH_IDLE_COUNT 10  // (2-255) Must be less than or equal to the busy count
#define ACCELERATION_TICKS_PER_SECOND 100
#define ADAPTIVE_MULTI_AXIS_STEP_SMOOTHING  // Default enabled. Comment to disable.
#define TOOL_LENGTH_OFFSET_AXIS Z_AXIS // Default z-axis. Valid values are X_AXIS, Y_AXIS, or Z_AXIS.
#define VARIABLE_SPINDLE // Default enabled. Comment to disable.
#define MINIMUM_JUNCTION_SPEED 0.0 // (mm/min)
#define MINIMUM_FEED_RATE 1.0 // (mm/min)
#define N_ARC_CORRECTION 12 // Integer (1-255)
#define ARC_ANGULAR_TRAVEL_EPSILON 5E-7 // Float (radians)
#define DWELL_TIME_STEP 50 // Integer (1-255) (milliseconds)
#define ENABLE_RESTORE_EEPROM_WIPE_ALL         // '$RST=*' Default enabled. Comment to disable.
#define ENABLE_RESTORE_EEPROM_DEFAULT_SETTINGS // '$RST=$' Default enabled. Comment to disable.
#define ENABLE_RESTORE_EEPROM_CLEAR_PARAMETERS // '$RST=#' Default enabled. Comment to disable.
#define ENABLE_BUILD_INFO_WRITE_COMMAND // '$I=' Default enabled. Comment to disable.
#define FORCE_BUFFER_SYNC_DURING_EEPROM_WRITE // Default enabled. Comment to disable.
#define FORCE_BUFFER_SYNC_DURING_WCO_CHANGE // Default enabled. Comment to disable.
#define PARKING_AXIS Z_AXIS // Define which axis that performs the parking motion
#define PARKING_TARGET -5.0 // Parking axis target. In mm, as machine coordinate [-max_travel,0].
#define PARKING_RATE 500.0 // Parking fast rate after pull-out in mm/min.
#define PARKING_PULLOUT_RATE 100.0 // Pull-out/plunge slow feed rate in mm/min.
#define PARKING_PULLOUT_INCREMENT 5.0 // Spindle pull-out and plunge distance in mm. Incremental distance.
#define DISABLE_LASER_DURING_HOLD // Default enabled. Comment to disable.
#define N_PIECES 4  // Integer (1-4). Number of piecewise lines used in script solution.
#define RPM_MAX  11686.4  // Max RPM of model. $30 > RPM_MAX will be limited to RPM_MAX.
#define RPM_MIN  202.5    // Min RPM of model. $31 < RPM_MIN will be limited to RPM_MIN.
#define RPM_POINT12  6145.4  // Used N_PIECES >=2. Junction point between lines 1 and 2.
#define RPM_POINT23  9627.8  // Used N_PIECES >=3. Junction point between lines 2 and 3.
#define RPM_POINT34  10813.9 // Used N_PIECES = 4. Junction point between lines 3 and 4.
#define RPM_LINE_A1  3.197101e-03  // Used N_PIECES >=1. A and B constants of line 1.
#define RPM_LINE_B1  -3.526076e-1
#define RPM_LINE_A2  1.722950e-2   // Used N_PIECES >=2. A and B constants of line 2.
#define RPM_LINE_B2  8.588176e+01
#define RPM_LINE_A3  5.901518e-02  // Used N_PIECES >=3. A and B constants of line 3.
#define RPM_LINE_B3  4.881851e+02
#define RPM_LINE_A4  1.203413e-01  // Used N_PIECES = 4. A and B constants of line 4.
#define RPM_LINE_B4  1.151360e+03
#define DUAL_AXIS_SELECT  X_AXIS  // Must be either X_AXIS or Y_AXIS
#define DUAL_AXIS_HOMING_FAIL_AXIS_LENGTH_PERCENT  5.0  // Float (percent)
#define DUAL_AXIS_HOMING_FAIL_DISTANCE_MAX  25.0  // Float (mm)
#define DUAL_AXIS_HOMING_FAIL_DISTANCE_MIN  2.5  // Float (mm)
#define DUAL_AXIS_CONFIG_PROTONEER_V3_51    // Uncomment to select. Comment other configs.

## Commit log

2020-03-08 Make BOM/assembly instructions generation work
    [frame_assembly.scad, main_assembly.scad, y_axis_holder.stl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]
2020-03-14 Y-axis motor mounting brackets v1
    [common_consts.scad, common_defs.scad, main_assembly.scad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]
2020-03-14 Update automatically generated files
    [y_motor_left_mount.stl, y_motor_right_mount.stl]
2020-03-14 Add y-idlers and belts
    [common_consts.scad, common_defs.scad, main_assembly.scad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]
2020-03-14 Docs+stls: y axis idler
    [y_idler.stl, y_idler_assembly.scad, y_motor_right_mount.stl]
2020-03-15 WIP y-carriage
    [common_consts.scad, main_assembly.scad, y_carriage_base_assembly.scad]
2020-03-15 Update the base y-carriage and docs
    [common_consts.scad, common_defs.scad, y_carriage_base.stl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]
2020-03-21 Don't do MPMD belts
    [common_consts.scad, common_defs.scad, main_assembly.scad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]
2020-03-21 Update to built model
    [angle_bracket.scad, y_carriage_base_assembly.scad]
2020-03-21 Update STLs and docs
    [y_carriage_base.stl, y_carriage_belt_clamp.stl, y_idler.stl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]
2020-03-21 Add constraints for rods
    [y_idler.stl, y_idler_assembly.scad, y_motor_assembly.scad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]
2020-03-21 Add limit switches for the y-axis
    [common_defs.scad, main_assembly.scad, y_carriage_base_assembly.scad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]
2020-03-21 Update docs for limit switches
    [y_carriage_base.stl, y_limit_switch.stl, y_limit_switch_hitter.stl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]
2020-03-22 Rearrange assemblies to generate saner docs (fix #2)
    [back_assembly.scad, frame_assembly.scad, front_assembly.scad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]
2020-03-28 Use M4 screws for y-idlers
    [y_idler.stl, y_idler_assembly.scad]
2020-03-29 WIP x-axis gantry
    [common_consts.scad, main_assembly.scad, x_axis_assembly.scad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]
2020-04-05 Add the x-carriage and laser module assembly
    [FisherPriceCNC.kicad_pcb, FisherPriceCNC.sch, electronics_assembly.scad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]
2020-04-10 Add GRBL config for an XY-only machine
2020-04-11 Wire holder for the x-axis
    [laser_wire_holder.stl, x_carriage_assembly.scad, x_carriage_front.stl]
2020-04-25 Electronics box
    [back_assembly.scad, electronics_assembly.scad, square_nut_lug.scad]
2020-04-25 Update docs
    [ele_box_base.stl, ele_box_top.stl, ele_bracket.stl]

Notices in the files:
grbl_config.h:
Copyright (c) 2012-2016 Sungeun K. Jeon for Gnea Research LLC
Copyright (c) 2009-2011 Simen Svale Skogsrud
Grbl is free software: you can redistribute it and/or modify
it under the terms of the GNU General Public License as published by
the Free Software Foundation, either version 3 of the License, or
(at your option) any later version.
